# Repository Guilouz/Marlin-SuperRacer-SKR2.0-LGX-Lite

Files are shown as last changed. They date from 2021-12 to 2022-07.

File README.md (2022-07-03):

Si vous aimez mon travail, n'hésitez pas à me soutenir en me payant une 🍺 ou un ☕. Merci 🙂

 Download (https://www.paypal.me/CyrilGuislain)

**Firmware Marlin configuré pour FLSUN Super Racer avec carte mère BigTreeTech SRK 2.0 et extrudeur Direct Drive Bondtech LGX Lite (moteur LDO-36STH20-1004AHG(XH))**<br />



<br />



<br />

## Téléchargement

**Firmware disponible [ici](https://github.com/Guilouz/Marlin-SuperRacer-SKR2.0-LGX-Lite/releases).**

Le firmware pour écran BigTreeTech TFT70 3.0 est disponible [ici](https://github.com/Guilouz/BTT-TFT70-SuperRacer).

## Support

Support disponible sur le serveur Discord de JSTECH à cette adresse : https://discord.gg/NS4zYd23dX

## ATTENTION

Lire attentivement ceci pour [SKR 2.0 Rev. A et Rev. B](https://docs.google.com/document/d/1IeKgfE2WIDjqH1fx5Yg7n1FOHVwhDFmDlZ-7QMlOEV0/edit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).

EDIT 06/12/2021 : En raison de la pénurie de composants, BigTreeTech utilise désormait une autre version de processeur `STM32F429VGT6` à la place du `STM32F407VGT6`. Il est donc nécessaire de changer l'environnement dans le fichier `platformio.ini` pour la compilation. Le firmware terminant par `F429` fourni dans la partie <a href="https://github.com/Guilouz/Marlin-SuperRacer-SKR2.0-LGX-Lite/releases">releases</a> est compatible avec cette nouvelle version.

<table>
<tr>
<td>
<br/>
</td>
<td>
default_envs = BIGTREE_SKR_2
</td>
</tr>
<tr>
<td>
<br/>
</td>
<td>
default_envs = BIGTREE_SKR_2_F429
</td>
</tr>
</table>

## Schema de câblage :

FLSUN SuperRacer SKR2

Capture d’écran 2021-12-08 à 00 44 42

## Principales fonctionnalités configurées :

- Support carte mère BigTreeTech SKR 2.0
- Support extrudeur Direct Drive Bondtech LGX Lite
- Support drivers TMC2209/TMC2226 configurés en UART
- Support écrans BigTreeTech
- Support Bed Leveling Bilinear 9 x 9 points
- Support Bilinear Subdivision
- Support M600 & Nozzle Park / Advanced Pause
- Support Babystepping
- Support Neopixels
- Support EEPROM
- Support PID Buse & Plateau
- Support protection thermique contre l'emballement
- Support S-Curve Acceleration
- Support de l'ajustement Delta Diagonal Rod Trim
- Support du Multi Volumes (ports microSD et USB fonctionnels)
- Support Firmware Auto Retract
- Support G26 - Mesh Validation Pattern
- Support G33 - Delta Auto Calibration
- Support du transfert de fichier binaire (transfert du fichier firmware à distance via Octoprint)
- Support des commandes d'action de l'hôte
- Activation du ventilateur de la hotend uniquement quand la chauffe dépasse 50°C
- Prise en charge de plusieurs volumes (microSD & USB)
- Prise en charge du partage multimédia USB
- Optimisation du buffer pour Octoprint
- Marlin en français

## Procédure d'installation :

- Copiez le fichier `firmware.bin` à la racine de la carte microSD (capacité max de 32Go, formatée en FAT32, taille d'unité d'allocation 4096).
- Imprimante éteinte, insérez la carte microSD dans le port dédié sur la carte mère et allumez l'imprimante.
- La procédure de flash démarre (sans rien afficher à l'écran) et dure quelques secondes.
- Vérifiez le contenu de la carte microSD, le fichier `firmware.bin` a été renommé en `FIRMWARE.CUR` ce qui indique que le flash s'est bien déroulé.
- Effectuez un reset EEPROM via `Menu` / `Options` / `Machine` / `EEPROM` / `Reset`.
- Lancez un PID Buse & Plateau via `Menu` / `Options` / `Machine` / `Tuning` / `PID`.
- Lancez une calibration de l'extrudeur via `Menu` / `Options` / `Machine` / `Tuning` / `Extrudeur`.
- Lancez une calibration Delta via `Menu` / `Mouvement` / `Calibrer`.
- Lancez un auto-nivellement via `Menu` / `Mouvement` / `ABL` / `Démarrer`.
- Réglez le Z-Offset via `Menu` / `Mouvement` / `ABL` / `Z-Offset`.
- Si vous voulez plus de précision ou régler des problèmes de cotes, suivez les instructions de ce fichier Excel : [Delta Calibration Calculator.zip](https://github.com/Guilouz/Marlin-SuperRacer-SKR2.0-LGX-Lite/files/8146625/Delta.Calibration.Calculator.zip)

## Fichiers STL et matériels nécessaires :

<table border="0">
 <tr>
 <td>
 
 </td>
 <td>
 <a href="https://github.com/Guilouz/Marlin-SuperRacer-SKR2.0-LGX-Lite/files/7798453/TFT70.Case.zip">TFT70 Case.zip</a>
 </td>
 <td>
 - Nécessite 4 vis M3x18 pour fixer la face avant et arrière de l'écran<br />
 - Nécessite 2 vis M3x12 pour fixer l'écran au support<br />
 - Nécessite 2 écrous M3 pour fixer l'écran au support<br />
 - Utilisation des vis stock pour fixer le support
 </td>
 <tr>
 <td>
 
 </td>
 <td>
 <a href="https://github.com/Guilouz/Marlin-SuperRacer-SKR2.0-LGX-Lite/files/7798455/Spool.Holder.zip">Spool Holder.zip</a>
 </td>
 <td>
 - Nécessite 4 vis M3x20<br />
 - Nécessite 4 roulements à billes 608ZZ
 </td>
 </tr>
 <tr>
 <td>
 
 </td>
 <td>
 <a href="https://github.com/Guilouz/Marlin-SuperRacer-SKR2.0-LGX-Lite/files/7798458/Filament.Sensor.Mount.zip">Filament Sensor Mount.zip</a>
 </td>
 <td>
- Utilisation des vis stock
 </td>
 </tr>
 <tr>
 <td>
 
 </td>
 <td>
 <a href="https://github.com/Guilouz/Marlin-SuperRacer-SKR2.0-LGX-Lite/files/7798459/SKR2.Plate.zip">SKR2 Plate.zip</a>
 </td>
 <td>
- Découpe nécessaire dans le châssis<br />
- Plaque à coller sur le châssis
 </td>
 </tr>
 <tr>
 <td>
 
 </td>
 <td>
 <a href="https://github.com/Guilouz/Marlin-SuperRacer-SKR2.0-LGX-Lite/files/7798461/Cable.Guide.zip">Cable Guide.zip</a>
 </td>
 <td>
- N/A
 </td>
 </tr>
 <tr>
 <td>
 
 </td>
 <td>
 <a href="https://github.com/Guilouz/Marlin-SuperRacer-SKR2.0-LGX-Lite/files/7798462/Neopixels.Mount.zip">Neopixels Mount.zip</a>
 </td>
 <td>
- Nécessite des colliers de serrage 2.5mm<br />
- Nécessite un fer à souder et de l'étain<br />
- Nécessite du câble 22 AWG (<a href="https://www.amazon.fr/gp/product/B089N4SWC1/ref=ppx_yo_dt_b_asin_title_o05_s00?ie=UTF8&psc=1">Lien</a>)<br />
- Nécessite un connecteur JST XH 2.54mm 3 pins et une pince à sertir (<a href="https://www.amazon.fr/connecteurs-PEBA-femelle-Adaptateur-Connecteur/dp/B08GR76H3D/?th=1">Lien</a>)<br />
- Nécessite un anneau de LED (<a href="https://fr.aliexpress.com/item/32825718399.html">Lien</a>, ou <a href="https://fr.aliexpress.com/item/32466976963.html">Lien</a>, ou <a href="https://fr.aliexpress.com/item/33032787658.html">Lien</a>)<br />
 </td>
 </tr>
 <tr>
 <td>
 
 </td>
 <td>
 <a href="https://www.thingiverse.com/thing:5138588">LGX Lite Support</a>
 </td>
 <td>
 - Nécessite 2 vis M3x12 pour fixer le LGX Lite au support<br />
 - Utilisation des vis stock pour fixer l'ensemble<br />
 - Nécessite 2 ventilateurs 5015 (optionnels)<br />
 - Nécessite 2 vis M3x16 pour les ventilateurs 5015 (optionnels)<br />
 - Nécessite 2 vis M3x20 pour les ventilateurs 5015 (optionnels)
 </td>
 </tr>
 </table>

## Réglages slicers recommandés :

**G-Code de démarrage :**

`G21 ; Unités en millimètres`<br />
`G90 ; Positionnement absolu`<br />
`M82 ; Axe E en mode absolu`<br />
`M140 S{material_bed_temperature} ; Température du plateau` (pour Cura)<br />
`M104 S{material_print_temperature} ; Température de la buse` (pour Cura)<br />
`M190 S{material_bed_temperature} ; Attente la température du plateau` (pour Cura)<br />
`M109 S{material_print_temperature} ; Attente de la température de la buse` (pour Cura)<br />
`G28 ; Origines des axes`<br />
`M420 S1 ; Activation du maillage`<br />
`; Descente de la Hotend et passage à la position de départ`<br />
`G1 Z150`<br />
`G1 X-130 Y0 Z0.4 F3000`<br />
`; Extrude environ 40mm en imprimant un arc de 90 degrés`<br />
`G3 X0 Y-130 I130 Z0.3 E40 F1500`<br />
`; Rétraction et déplacement de la hotend vers le haut`<br />
`G92 E0`<br />
`G1 E-1.5 F1800`<br />
`G0 Z0.5`<br />
`G1 E0 F300`

**G-Code de fin :**

`G91 ; Positionnement relatif`<br />
`G1 E-1 F300 ; Rétraction avant déplacement de la hotend vers le haut`<br />
`G1 Z+5 E-5 F6000 ; Déplacement de la hotend vers le haut`<br />
`G28 X0 Y0 ; Origines des axes`<br />
`G90 ; Positionnement absolu`<br />
`G92 E0 ; Réinitialisation de l'extrudeur`<br />
`M104 S0 ; Arrêt de la chauffe de la buse`<br />
`M140 S0 ; Arrêt de la chauffe du plateau`<br />
`M107 ; Arrêt des ventilateurs`<br />
`M84 ; Désactivation des moteurs`

**Rétraction :**

- Distance : `1.2 mm`
- Vitesse : `35 mm/s`

## Changements éventuels :

Ce firmware est configuré pour une carte mère BigTreeTech SKR 2.0 Rev. B avec MCU STM32F407VGT6 et extrudeur Bondtech LGX. Certains changements peuvent être effectués si vous disposez d'autres équipements.

  - Pour changer la langue de Marlin en anglais, définissez cette valeur :
    - Dans Configuration.h : `#define LCD_LANGUAGE en`

  - Si ` HEATBLOCK Trianglelab CHC Pro (104NT-4-R025H42G)`, définissez ces valeurs :
    - Dans Configuration.h : `#define TEMP_SENSOR_0 5`
    - Dans Configuration.h : `#define DEFAULT_Kp 13.0091`
    - Dans Configuration.h : `#define DEFAULT_Ki 1.9370`
    - Dans Configuration.h : `#define DEFAULT_Kd 21.8422`

  - Si `EXTRUDEUR FLSUN STOCK / BONDTECH BMG (BOWDEN)`, définissez ces valeurs :
    - Dans Configuration.h : `#define DEFAULT_AXIS_STEPS_PER_UNIT   { 80, 80, 80, 415 }`
    - Dans Configuration.h : `#define INVERT_E0_DIR true`
    - Dans Configuration_adv.h : `#define E0_CURRENT      1050`
    - Dans Configuration_adv.h : `#define FILAMENT_CHANGE_UNLOAD_LENGTH      350`
    - Dans Configuration_adv.h : `#define FILAMENT_CHANGE_FAST_LOAD_LENGTH     350`

  - Si `EXTRUDEUR OMG-V2-S (BOWDEN)`, définissez ces valeurs :
    - Dans Configuration.h : `#define DEFAULT_AXIS_STEPS_PER_UNIT   { 80, 80, 80, 385 }`
    - Dans Configuration.h : `#define INVERT_E0_DIR true`
    - Dans Configuration_adv.h : `#define E0_CURRENT      1050`
    - Dans Configuration_adv.h : `#define FILAMENT_CHANGE_UNLOAD_LENGTH      350`
    - Dans Configuration_adv.h : `#define FILAMENT_CHANGE_FAST_LOAD_LENGTH     350`

  - Si `EXTRUDEUR BONDTECH LGX (BOWDEN)`, définissez ces valeurs :
    - Dans Configuration.h : `#define DEFAULT_AXIS_STEPS_PER_UNIT   { 80, 80, 80, 400 }`
    - Dans Configuration.h : `#define INVERT_E0_DIR false`
    - Dans Configuration_adv.h : `#define E0_CURRENT      650`
    - Dans Configuration_adv.h : `#define FILAMENT_CHANGE_UNLOAD_LENGTH      350`
    - Dans Configuration_adv.h : `#define FILAMENT_CHANGE_FAST_LOAD_LENGTH     350`

  - Si `EXTRUDEUR BONDTECH LGX LITE (DIRECT DRIVE)`, définissez ces valeurs :
    - Dans Configuration.h : `#define DEFAULT_AXIS_STEPS_PER_UNIT   { 80, 80, 80, 562 }`
    - Dans Configuration.h : `#define INVERT_E0_DIR false`
    - Dans Configuration_adv.h : `#define E0_CURRENT      650`
    - Dans Configuration_adv.h : `#define FILAMENT_CHANGE_UNLOAD_LENGTH      70`
    - Dans Configuration_adv.h : `#define FILAMENT_CHANGE_FAST_LOAD_LENGTH     70`

  - Si `MKS ROBIN NANO V3`, définissez ces valeurs :
    - Dans platformio.ini : `default_envs = mks_robin_nano_v3_usb_flash_drive_msc`
    - Dans Configuration.h : `#define MOTHERBOARD BOARD_MKS_ROBIN_NANO_V3`
    - Dans Configuration.h : `#define SERIAL_PORT -1`
    - Dans Configuration.h : `#define SERIAL_PORT_2 3`
    - Dans Configuration.h : `#define Z_MIN_PROBE_USES_Z_MIN_ENDSTOP_PIN`
    - Dans Configuration.h : `//#define Z_MIN_PROBE_PIN PA0`
    - Dans Configuration.h : `//#define NEOPIXEL_LED`
    - Dans Configuration_adv.h : `#define E0_AUTO_FAN_PIN PB0`
    - Dans Configuration_adv.h : `#define DISABLE_DRIVER_SAFE_POWER_PROTECT`
    - Dans pins_MKS_ROBIN_NANO_V3_common.h : `#define FAN_PIN PB1`
    - Dans pins_MKS_ROBIN_NANO_V3_common.h : `#define FAN1_PIN PC14`

Il est également nécessaire de déplacer le branchement des ventilateurs de refroidissement du port `FAN1` vers le port `FAN2`.

Un pack complet avec firmwares est disponible <a href="https://drive.google.com/file/d/1qiMYBQkulEuOpUn5UmmUM7sLWNKS4bEW/view?usp=sharing">ici</a>.
    
  - Si `SKR 1.3`, définissez ces valeurs :
    - Dans platformio.ini : `default_envs = LPC1768`
    - Dans Configuration.h : `#define MOTHERBOARD BOARD_BTT_SKR_V1_3`
    - Dans Configuration.h : `#define SERIAL_PORT -1`
    - Dans Configuration.h : `#define SERIAL_PORT_2 0`
    - Dans Configuration.h : `#define Z_MIN_PROBE_USES_Z_MIN_ENDSTOP_PIN`
    - Dans Configuration.h : `//#define Z_MIN_PROBE_PIN PA0`
    - Dans Configuration.h : `//#define NEOPIXEL_LED`
    - Dans Configuration_adv.h : `#define E0_AUTO_FAN_PIN P2_04`
    - Dans Configuration_adv.h : `//#define MULTI_VOLUME`
    - Dans Configuration_adv.h : `//#define USB_FLASH_DRIVE_SUPPORT`
    - Dans Configuration_adv.h : `#define DISABLE_DRIVER_SAFE_POWER_PROTECT`
    
  - Si `SKR 1.4`, définissez ces valeurs :
    - Dans platformio.ini : `default_envs = LPC1768`
    - Dans Configuration.h : `#define MOTHERBOARD BOARD_BTT_SKR_V1_4`
    - Dans Configuration.h : `#define SERIAL_PORT -1`
    - Dans Configuration.h : `#define SERIAL_PORT_2 0`
    - Dans Configuration.h : `#define Z_MIN_PROBE_PIN P1_25` Le palpeur doit être branché sur le port E1DET
    - Dans Configuration.h : `//#define NEOPIXEL_LED`
    - Dans Configuration_adv.h : `#define E0_AUTO_FAN_PIN P2_04`
    - Dans Configuration_adv.h : `//#define MULTI_VOLUME`
    - Dans Configuration_adv.h : `//#define USB_FLASH_DRIVE_SUPPORT`
    - Dans Configuration_adv.h : `#define DISABLE_DRIVER_SAFE_POWER_PROTECT`
    
  - Si `SKR 1.4 Turbo`, définissez ces valeurs :
    - Dans platformio.ini : `default_envs = LPC1769`
    - Dans Configuration.h : `#define MOTHERBOARD BOARD_BTT_SKR_V1_4_TURBO`
    - Dans Configuration.h : `#define SERIAL_PORT -1`
    - Dans Configuration.h : `#define SERIAL_PORT_2 0`
    - Dans Configuration.h : `#define Z_MIN_PROBE_PIN P1_25` Le palpeur doit être branché sur le port E1DET
    - Dans Configuration_adv.h : `#define E0_AUTO_FAN_PIN P2_04`
    - Dans Configuration_adv.h : `//#define MULTI_VOLUME`
    - Dans Configuration_adv.h : `//#define USB_FLASH_DRIVE_SUPPORT`
    - Dans Configuration_adv.h : `#define DISABLE_DRIVER_SAFE_POWER_PROTECT`
    
  - Si `SKR 2.0 Rev. A`, définissez ces valeurs :
    - Dans Configuration.h : `#define MOTHERBOARD BOARD_BTT_SKR_V2_0_REV_A`
    - Dans Configuration_adv.h : `#define DISABLE_DRIVER_SAFE_POWER_PROTECT` en vous assurant d'avoir vérifier ceci : [SKR 2.0 Rev. A et Rev. B](https://docs.google.com/document/d/1IeKgfE2WIDjqH1fx5Yg7n1FOHVwhDFmDlZ-7QMlOEV0/edit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).

  - Si `SKR 2.0 avec MCU STM32F429VGT6`, définissez ces valeurs :
    - Dans platformio.ini : `default_envs = BIGTREE_SKR_2_F429`
  
Recompilez ensuite le firmware à l'aide de VSCode et PlatformIO (voir [ici](https://marlinfw.org/docs/basics/install_platformio_vscode.html)).

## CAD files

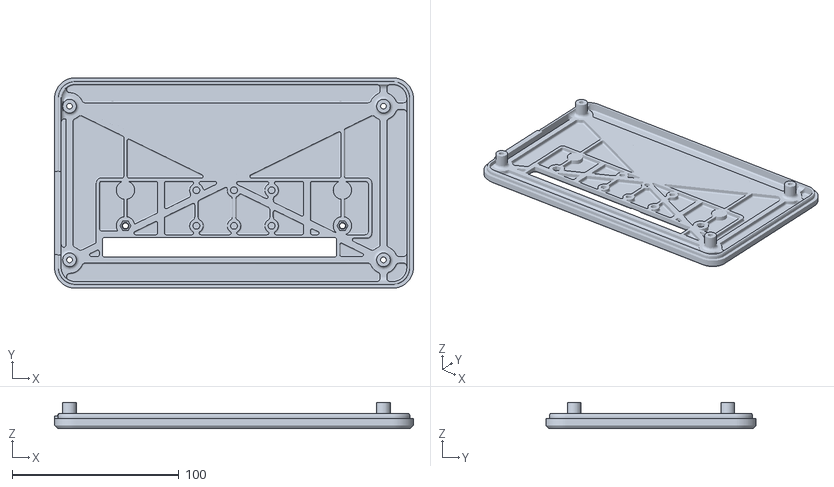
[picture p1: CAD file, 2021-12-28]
_STL/TFT70/V2/TFT70_Rear_Panel_V2.stl
215.0 x 126.0 x 15.8

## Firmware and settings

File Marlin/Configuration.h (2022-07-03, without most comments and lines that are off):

#pragma once
#define CONFIGURATION_H_VERSION 02010000
#define STRING_CONFIG_H_AUTHOR "(Cyril Guislain, Super Racer - SKR 2.0 - LGX Lite)" // Who made the changes.
#define CUSTOM_VERSION_FILE Version.h // Path from the root directory (no quotes)
#define SHOW_BOOTSCREEN
  #define MOTHERBOARD BOARD_BTT_SKR_V2_0_REV_B
#define SERIAL_PORT 1
#define BAUDRATE 250000
#define SERIAL_PORT_2 -1
#define CUSTOM_MACHINE_NAME "Super Racer"
#define X_DRIVER_TYPE  TMC2209
#define Y_DRIVER_TYPE  TMC2209
#define Z_DRIVER_TYPE  TMC2209
#define E0_DRIVER_TYPE TMC2209
#define EXTRUDERS 1
#define DEFAULT_NOMINAL_FILAMENT_DIA 1.75
#define TEMP_SENSOR_0 11
#define TEMP_SENSOR_1 0
#define TEMP_SENSOR_2 0
#define TEMP_SENSOR_3 0
#define TEMP_SENSOR_4 0
#define TEMP_SENSOR_5 0
#define TEMP_SENSOR_6 0
#define TEMP_SENSOR_7 0
#define TEMP_SENSOR_BED 11
#define TEMP_SENSOR_PROBE 0
#define TEMP_SENSOR_CHAMBER 0
#define TEMP_SENSOR_COOLER 0
#define TEMP_SENSOR_BOARD 0
#define TEMP_SENSOR_REDUNDANT 0
#define DUMMY_THERMISTOR_998_VALUE  25
#define DUMMY_THERMISTOR_999_VALUE 100
#define TEMP_RESIDENCY_TIME         2  // (seconds) Time to wait for hotend to "settle" in M109
#define TEMP_WINDOW                  1  // (°C) Temperature proximity for the "temperature reached" timer
#define TEMP_HYSTERESIS              3  // (°C) Temperature proximity considered "close enough" to the target
#define TEMP_BED_RESIDENCY_TIME     2  // (seconds) Time to wait for bed to "settle" in M190
#define TEMP_BED_WINDOW              1  // (°C) Temperature proximity for the "temperature reached" timer
#define TEMP_BED_HYSTERESIS          3  // (°C) Temperature proximity considered "close enough" to the target
#define TEMP_CHAMBER_RESIDENCY_TIME 10  // (seconds) Time to wait for chamber to "settle" in M191
#define TEMP_CHAMBER_WINDOW          1  // (°C) Temperature proximity for the "temperature reached" timer
#define TEMP_CHAMBER_HYSTERESIS      3  // (°C) Temperature proximity considered "close enough" to the target
#if TEMP_SENSOR_REDUNDANT
  #define TEMP_SENSOR_REDUNDANT_SOURCE    E1  // The sensor that will provide the redundant reading.
  #define TEMP_SENSOR_REDUNDANT_TARGET    E0  // The sensor that we are providing a redundant reading for.
  #define TEMP_SENSOR_REDUNDANT_MAX_DIFF  10  // (°C) Temperature difference that will trigger a print abort.
#endif
#define HEATER_0_MINTEMP   5
#define HEATER_1_MINTEMP   5
#define HEATER_2_MINTEMP   5
#define HEATER_3_MINTEMP   5
#define HEATER_4_MINTEMP   5
#define HEATER_5_MINTEMP   5
#define HEATER_6_MINTEMP   5
#define HEATER_7_MINTEMP   5
#define BED_MINTEMP        5
#define CHAMBER_MINTEMP    5
#define HEATER_0_MAXTEMP 275
#define HEATER_1_MAXTEMP 275
#define HEATER_2_MAXTEMP 275
#define HEATER_3_MAXTEMP 275
#define HEATER_4_MAXTEMP 275
#define HEATER_5_MAXTEMP 275
#define HEATER_6_MAXTEMP 275
#define HEATER_7_MAXTEMP 275
#define BED_MAXTEMP      115
#define CHAMBER_MAXTEMP  60
#define HOTEND_OVERSHOOT 15   // (°C) Forbid temperatures over MAXTEMP - OVERSHOOT
#define BED_OVERSHOOT    10   // (°C) Forbid temperatures over MAXTEMP - OVERSHOOT
#define COOLER_OVERSHOOT  2   // (°C) Forbid temperatures closer than OVERSHOOT
#define PIDTEMP          // See the PID Tuning Guide at https://reprap.org/wiki/PID_Tuning
#define BANG_MAX 255     // Limits current to nozzle while in bang-bang mode; 255=full current
#define PID_MAX BANG_MAX // Limits current to nozzle while PID is active (see PID_FUNCTIONAL_RANGE below); 255=full current
#define PID_K1 0.95      // Smoothing factor within any PID loop
    #define DEFAULT_Kp 21.9886
    #define DEFAULT_Ki 1.8834
    #define DEFAULT_Kd 64.1793
#define PIDTEMPBED
#define MAX_BED_POWER 255 // limits duty cycle to bed; 255=full current
  #define DEFAULT_bedKp 87.5094
  #define DEFAULT_bedKi 16.8303
  #define DEFAULT_bedKd 303.3368
#define MAX_CHAMBER_POWER 255 // limits duty cycle to chamber heater; 255=full current
  #define PID_FUNCTIONAL_RANGE 10 // If the temperature difference between the target temperature and the actual temperature
#define PREVENT_COLD_EXTRUSION
#define EXTRUDE_MINTEMP 180
#define PREVENT_LENGTHY_EXTRUDE
#define EXTRUDE_MAXLENGTH 1500
#define THERMAL_PROTECTION_HOTENDS // Enable thermal protection for all extruders
#define THERMAL_PROTECTION_BED     // Enable thermal protection for the heated bed
#define THERMAL_PROTECTION_CHAMBER // Enable thermal protection for the heated chamber
#define THERMAL_PROTECTION_COOLER  // Enable thermal protection for the laser cooling
#define DELTA
  #define DELTA_SEGMENTS_PER_SECOND 160
  #define DELTA_AUTO_CALIBRATION
    #define DELTA_CALIBRATION_DEFAULT_POINTS 4
    #define PROBE_MANUALLY_STEP 0.05      // (mm)
  #define DELTA_PRINTABLE_RADIUS 132    // (mm)
  #define DELTA_DIAGONAL_ROD 315       // (mm)
  #define DELTA_HEIGHT 330            // (mm) Get this value from G33 auto calibrate
  #define DELTA_ENDSTOP_ADJ { 0.0, 0.0, 0.0 } // Get these values from G33 auto calibrate
  #define DELTA_RADIUS 152              // (mm) Get this value from G33 auto calibrate
  #define DELTA_TOWER_ANGLE_TRIM { 0.0000, 0.0000, 0.0000 } // Get these values from G33 auto calibrate
  #define DELTA_DIAGONAL_ROD_TRIM_TOWER { 0.0, 0.0, 0.0 }
#define USE_ZMIN_PLUG
#define USE_XMAX_PLUG
#define USE_YMAX_PLUG
#define USE_ZMAX_PLUG
#define ENDSTOPPULLUPS
#define X_MIN_ENDSTOP_INVERTING false // Set to true to invert the logic of the endstop.
#define Y_MIN_ENDSTOP_INVERTING false // Set to true to invert the logic of the endstop.
#define Z_MIN_ENDSTOP_INVERTING true // Set to true to invert the logic of the endstop.
#define I_MIN_ENDSTOP_INVERTING false // Set to true to invert the logic of the endstop.
#define J_MIN_ENDSTOP_INVERTING false // Set to true to invert the logic of the endstop.
#define K_MIN_ENDSTOP_INVERTING false // Set to true to invert the logic of the endstop.
#define U_MIN_ENDSTOP_INVERTING false // Set to true to invert the logic of the endstop.
#define V_MIN_ENDSTOP_INVERTING false // Set to true to invert the logic of the endstop.
#define W_MIN_ENDSTOP_INVERTING false // Set to true to invert the logic of the endstop.
#define X_MAX_ENDSTOP_INVERTING false // Set to true to invert the logic of the endstop.
#define Y_MAX_ENDSTOP_INVERTING false // Set to true to invert the logic of the endstop.
#define Z_MAX_ENDSTOP_INVERTING false // Set to true to invert the logic of the endstop.
#define I_MAX_ENDSTOP_INVERTING false // Set to true to invert the logic of the endstop.
#define J_MAX_ENDSTOP_INVERTING false // Set to true to invert the logic of the endstop.
#define K_MAX_ENDSTOP_INVERTING false // Set to true to invert the logic of the endstop.
#define U_MAX_ENDSTOP_INVERTING false // Set to true to invert the logic of the endstop.
#define V_MAX_ENDSTOP_INVERTING false // Set to true to invert the logic of the endstop.
#define W_MAX_ENDSTOP_INVERTING false // Set to true to invert the logic of the endstop.
#define Z_MIN_PROBE_ENDSTOP_INVERTING true // Set to true to invert the logic of the probe.
#define DEFAULT_XYZ_STEPS_PER_UNIT 80
#define DEFAULT_AXIS_STEPS_PER_UNIT   { 80, 80, 80, 572.90 }
#define DEFAULT_MAX_FEEDRATE          { 200, 200, 200, 120 }
#define DEFAULT_MAX_ACCELERATION      { 6000, 6000, 6000, 1500 }
#define DEFAULT_ACCELERATION          2500    // X, Y, Z and E acceleration for printing moves
#define DEFAULT_RETRACT_ACCELERATION  2000    // E acceleration for retracts
#define DEFAULT_TRAVEL_ACCELERATION   2800    // X, Y, Z acceleration for travel (non printing) moves
#define CLASSIC_JERK
  #define DEFAULT_XJERK 10.0
  #define DEFAULT_YJERK 10.0
  #define DEFAULT_ZJERK  10.0
#define DEFAULT_EJERK    2.5  // May be used by Linear Advance
#define S_CURVE_ACCELERATION
#define Z_MIN_PROBE_PIN PA0 // Pin 32 is the RAMPS default
#define FIX_MOUNTED_PROBE
#define NOZZLE_TO_PROBE_OFFSET { 0, 0, -16.5 }
#define PROBING_MARGIN 5
#define XY_PROBE_FEEDRATE (34*60)
#define Z_PROBE_FEEDRATE_FAST (30*60)
#define Z_PROBE_FEEDRATE_SLOW (Z_PROBE_FEEDRATE_FAST / 2)
#define Z_CLEARANCE_DEPLOY_PROBE   5 // Z Clearance for Deploy/Stow
#define Z_CLEARANCE_BETWEEN_PROBES  2 // Z Clearance between probe points
#define Z_CLEARANCE_MULTI_PROBE     15 // Z Clearance between multiple probes
#define Z_PROBE_LOW_POINT          -25 // Farthest distance below the trigger-point to go before stopping
#define Z_PROBE_OFFSET_RANGE_MIN -30
#define Z_PROBE_OFFSET_RANGE_MAX 30
#define PROBING_FANS_OFF          // Turn fans off when probing
#define PROBING_ESTEPPERS_OFF     // Turn all extruder steppers off when probing
#define X_ENABLE_ON 0
#define Y_ENABLE_ON 0
#define Z_ENABLE_ON 0
#define E_ENABLE_ON 0 // For all extruders
#define DISABLE_X false
#define DISABLE_Y false
#define DISABLE_Z false
#define DISABLE_E false             // Disable the extruder when not stepping
#define DISABLE_INACTIVE_EXTRUDER   // Keep only the active extruder enabled
#define INVERT_X_DIR false
#define INVERT_Y_DIR false
#define INVERT_Z_DIR false
#define INVERT_E0_DIR false
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

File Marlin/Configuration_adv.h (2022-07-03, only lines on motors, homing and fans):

#define E0_AUTO_FAN_PIN PB4
#define E1_AUTO_FAN_PIN -1
#define E2_AUTO_FAN_PIN -1
#define E3_AUTO_FAN_PIN -1
#define E4_AUTO_FAN_PIN -1
#define E5_AUTO_FAN_PIN -1
#define E6_AUTO_FAN_PIN -1
#define E7_AUTO_FAN_PIN -1
#define CHAMBER_AUTO_FAN_PIN -1
#define COOLER_AUTO_FAN_PIN -1
#define HOMING_BUMP_MM      { 5, 5, 5 }       // (linear=mm, rotational=°) Backoff from endstops after first bump
#define HOMING_BUMP_DIVISOR { 10, 10, 10 }       // Re-Bump Speed Divisor (Divides the Homing Feedrate)
#define MICROSTEP_MODES { 16, 16, 16, 16, 16, 16 } // [1,2,4,8,16]
#define ADVANCED_OK
#define ADVANCED_PAUSE_FEATURE
  #define ADVANCED_PAUSE_PURGE_FEEDRATE        3  // (mm/s) Extrude feedrate (after loading). Should be slower than load feedrate.
  #define ADVANCED_PAUSE_PURGE_LENGTH         50  // (mm) Length to extrude after loading.
  #define ADVANCED_PAUSE_RESUME_PRIME          0  // (mm) Extra distance to prime nozzle after returning from park.
  #define ADVANCED_PAUSE_FANS_PAUSE             // Turn off print-cooling fans while the machine is paused.
  #define HOME_BEFORE_FILAMENT_CHANGE           // If needed, home before parking for filament change
    #define X_CURRENT       1050        // (mA) RMS current. Multiply by 1.414 for peak current.
    #define X_CURRENT_HOME  X_CURRENT  // (mA) RMS current for sensorless homing
    #define X_MICROSTEPS     16        // 0..256
    #define Y_CURRENT       1050
    #define Y_CURRENT_HOME  Y_CURRENT
    #define Y_MICROSTEPS     16
    #define Z_CURRENT       1050
    #define Z_CURRENT_HOME  Z_CURRENT
    #define Z_MICROSTEPS     16
    #define E0_CURRENT      650
    #define E0_MICROSTEPS    16
    #define CURRENT_STEP_DOWN     50  // [mA]
    #define REPORT_CURRENT_CHANGE
  #define X_HYBRID_THRESHOLD     100  // [mm/s]
  #define X2_HYBRID_THRESHOLD    100
  #define Y_HYBRID_THRESHOLD     100
  #define Y2_HYBRID_THRESHOLD    100
  #define Z_HYBRID_THRESHOLD       3
  #define Z2_HYBRID_THRESHOLD      3
  #define Z3_HYBRID_THRESHOLD      3
  #define Z4_HYBRID_THRESHOLD      3
  #define I_HYBRID_THRESHOLD       3  // [linear=mm/s, rotational=°/s]
  #define J_HYBRID_THRESHOLD       3  // [linear=mm/s, rotational=°/s]
  #define K_HYBRID_THRESHOLD       3  // [linear=mm/s, rotational=°/s]
  #define U_HYBRID_THRESHOLD       3  // [mm/s]
  #define V_HYBRID_THRESHOLD       3
  #define W_HYBRID_THRESHOLD       3
  #define E0_HYBRID_THRESHOLD     30
  #define E1_HYBRID_THRESHOLD     30
  #define E2_HYBRID_THRESHOLD     30
  #define E3_HYBRID_THRESHOLD     30
  #define E4_HYBRID_THRESHOLD     30
  #define E5_HYBRID_THRESHOLD     30
  #define E6_HYBRID_THRESHOLD     30
  #define E7_HYBRID_THRESHOLD     30

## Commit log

2021-08-04 Initial release
    [Configuration.h, Configuration_adv.h, LED Support.stl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]
2021-08-16 Update 16-08-2021
    [Configuration.h]
2021-08-17 Update 17-08-2021
    [Configuration.h, Configuration_adv.h]
2021-09-05 Update 05-09-2021
    [Configuration.h, Configuration_adv.h]
2021-09-11 Update 12-09-2021
    [Configuration.h, Configuration_adv.h]
2021-10-01 Update 01-10-2021
    [Configuration.h, Configuration_adv.h]
2021-10-04 Update 04-10-2021
    [Configuration.h, Configuration_adv.h]
2021-10-19 Update 20-10-2021
    [Configuration_adv.h, esp32.csv]
2021-11-03 Update 03-11-2021
    [Configuration.h, Configuration_adv.h]
2021-11-26 Update 26-11-2021
    [Configuration.h, Configuration_adv.h]
2021-12-06 Update 06-12-2021
    [Configuration.h, Configuration_adv.h]
2021-12-28 Update 28-12-2021
    [Configuration.h, Configuration_adv.h]
2021-12-28 New TFT70 Support
    [TFT70_Front_Panel.stl, TFT70_Front_Panel_V2.stl, TFT70_Hole_Cover.stl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]
2021-12-31 Update 31-12-2021
    [Configuration.h, Configuration_adv.h]
2022-01-01 Add STL
    [Bolt.stl, Cable_Guide_1.stl, Cable_Guide_2.stl]
2022-01-01 Update STL
    [TFT70_Front_Panel_V2.stl, TFT70_Hole_Cover.stl, TFT70_Rear_Panel.stl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]
2022-01-02 Update repo
    [Bolt.stl, Cable_Guide_1.stl, Cable_Guide_2.stl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]
2022-01-09 Update 09-01-2022
    [Configuration.h, Configuration_adv.h]
2022-01-30 Update 30-01-2022
    [Configuration.h, Configuration_adv.h]
2022-02-12 Update 12-02-2022
    [Configuration.h, Configuration_adv.h]
2022-02-26 Update 26-02-2022
    [Configuration.h, Configuration_adv.h]
2022-03-11 Update 11-03-2022
    [Configuration.h, Configuration_adv.h]
2022-03-24 Update 24-03-2022
    [Configuration_adv.h]
2022-04-06 Update 07-04-2022
    [Configuration.h, Configuration_adv.h]
2022-04-11 Update 11-04-2022
    [Configuration.h, Configuration_adv.h]
2022-04-29 Update 29-04-2022
    [Configuration.h]
2022-04-30 Update 30-04-2022
    [Configuration.h]
2022-05-18 Update 18-05-2022
    [Configuration.h, Configuration_adv.h]
2022-05-31 Update 31-05-2022
    [Configuration.h, Configuration_adv.h]
2022-06-04 Update 06-04-2022
    [Configuration.h, Configuration_adv.h]
2022-07-03 Update 03-07-2022
    [Configuration.h, Configuration_adv.h]

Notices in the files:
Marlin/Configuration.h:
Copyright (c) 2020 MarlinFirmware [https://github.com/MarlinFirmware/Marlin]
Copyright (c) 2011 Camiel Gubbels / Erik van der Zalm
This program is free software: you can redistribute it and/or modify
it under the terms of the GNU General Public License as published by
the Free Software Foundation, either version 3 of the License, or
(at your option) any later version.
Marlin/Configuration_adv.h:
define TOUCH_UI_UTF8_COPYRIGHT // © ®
